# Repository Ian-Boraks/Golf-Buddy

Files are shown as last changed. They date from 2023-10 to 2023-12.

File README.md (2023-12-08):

- [Overview](#overview)
  - [Project Photos](#project-photos)
    - [Launcher](#launcher)
    - [Hole](#hole)
- [Hardware](#hardware)
  - [BOM](#bom)
  - [CAD](#cad)
    - [Laser Cut Parts](#laser-cut-parts)
  - [Electronics](#electronics)
    - [Wiring Diagram Launcher](#wiring-diagram-launcher)
    - [Wiring Diagram Hole](#wiring-diagram-hole)
- [Development](#development)
  - [RFID](#rfid)
    - [Code Snippets](#code-snippets)
  - [Launcher](#launcher-1)
    - [Code Snippets](#code-snippets-1)
  - [Hole](#hole-1)
    - [Code Snippets](#code-snippets-2)
- [Skills Beyond](#skills-beyond)
  - [Fernando](#fernando)
  - [Ian](#ian)

---

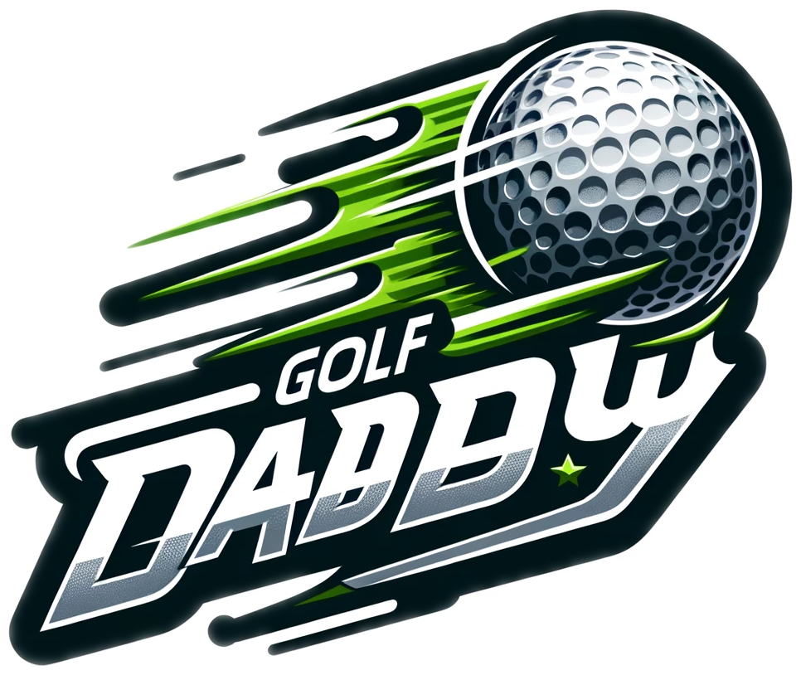
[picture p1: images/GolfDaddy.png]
Golf Buddy


[Demo Video (https://youtu.be/wagic4B7uYY)](https://youtu.be/wagic4B7uYY)
[RFID Video (https://youtu.be/jHi_h-PA1bc)](https://youtu.be/jHi_h-PA1bc)

# Overview

Welcome to the project documentation for an innovative addition to the world of mini golf: a High-Speed Golf Ball Shooter. This project began with a simple yet ambitious goal: to enhance the traditional golfing experience, particularly in the realm of putting. Our initial vision was to develop a tool that would assist golfers in refining their putting skills in a competitive and engaging manner. However, as we delved deeper into the project, our focus shifted, leading us to a more dynamic and playful interpretation of golfing aids.

**Main Reasons for Project Shift:**

1. Our motor was too powerful for the golf ball. We were unable to tune the motor speed too produce reasonable ball speeds.
2. Our RFID reader was unable to read the RFID tags on the golf balls. We were unable to find a solution to this problem that would be cost feasible with our limited budget.
3. The ball return mechanism was too complex for our limited time frame.

## Project Photos

### Launcher

\
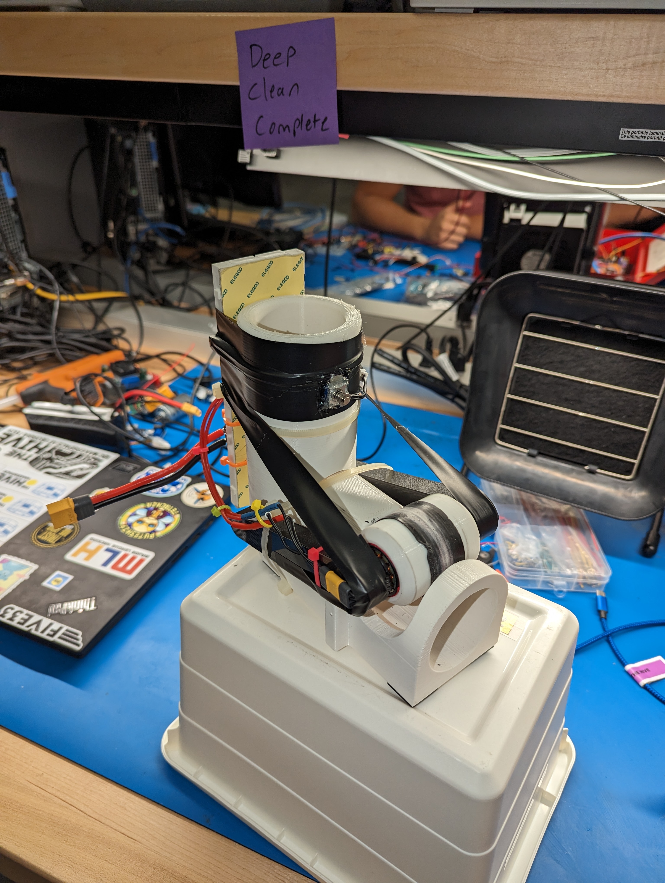
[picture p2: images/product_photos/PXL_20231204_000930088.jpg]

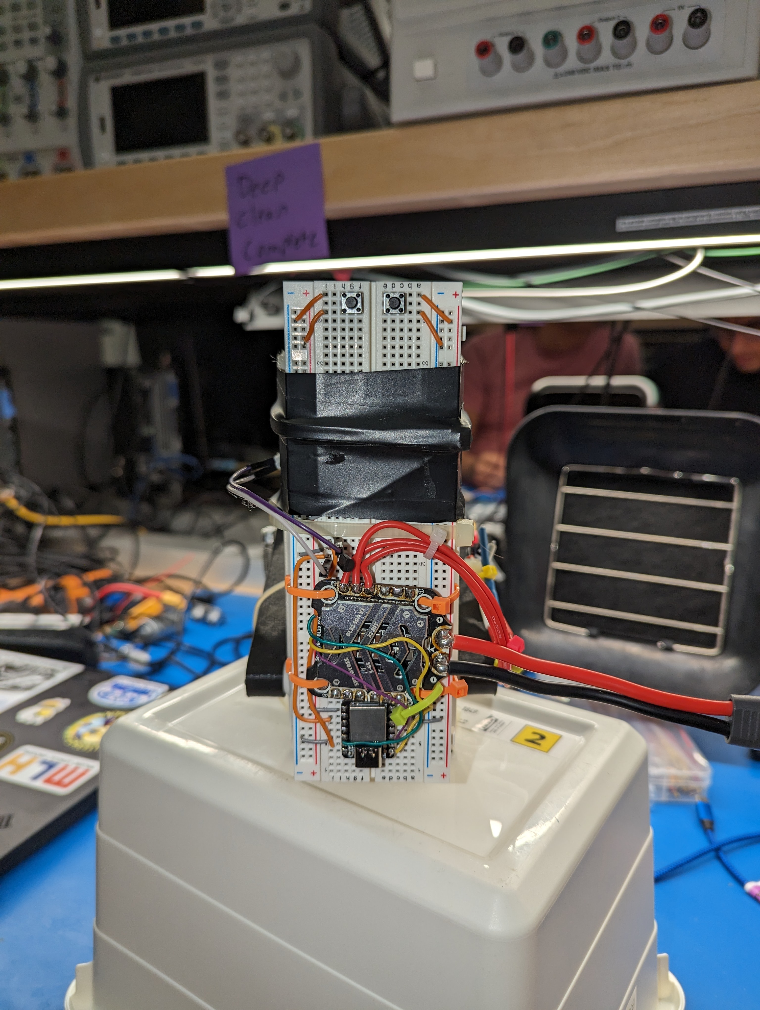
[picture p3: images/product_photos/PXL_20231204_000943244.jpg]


### Hole

\
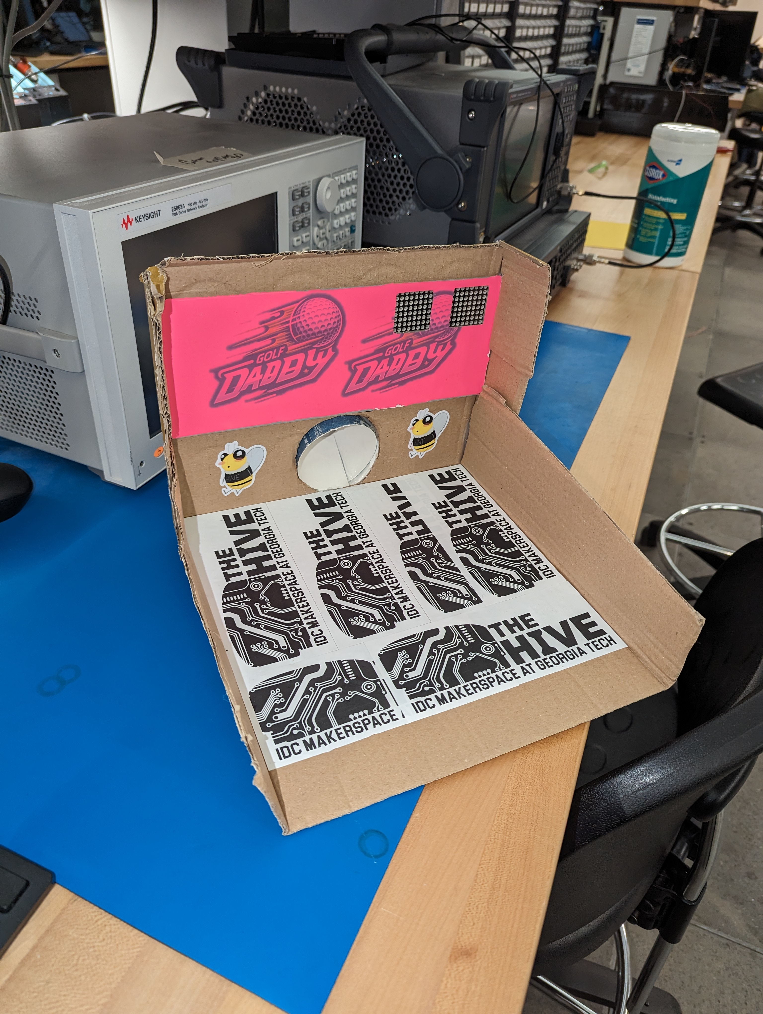
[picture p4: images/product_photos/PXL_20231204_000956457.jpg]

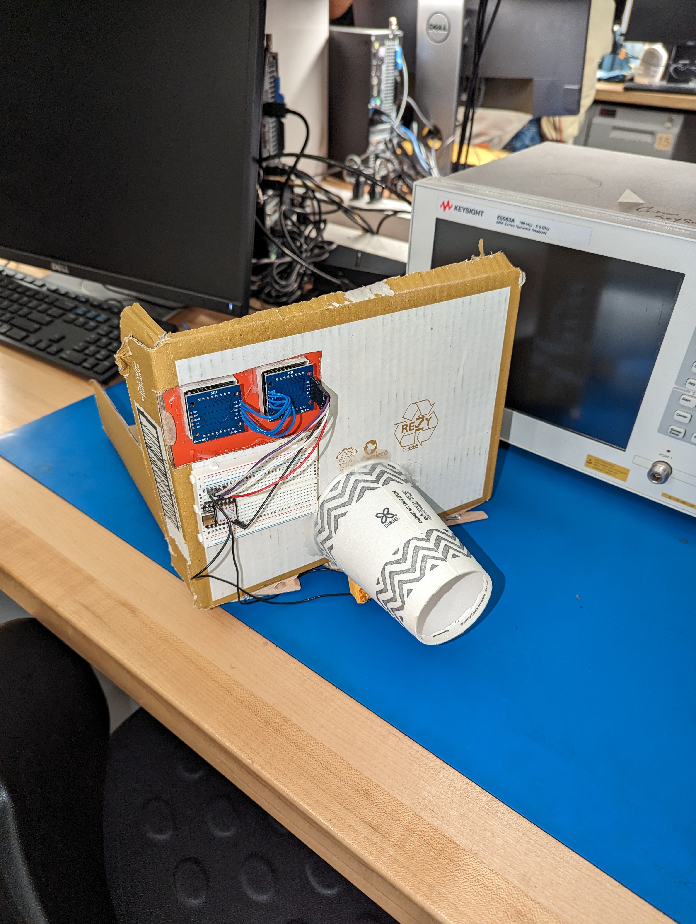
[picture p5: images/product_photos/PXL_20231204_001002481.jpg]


# Hardware

## BOM

| Part | Quantity | Price  |
| --- | --- | --- |
| Seeduino Xiao | 2 | $5.90  |
| NeoPixel Matrix  | 2 | $9.95  |
| 6s LiPo Battery  | 1 | $30.00 |
| ESC SpeedyBee | 1 | $60.00 |
| Bearings | 4 | $10.00 |
| 3D Printed Parts | 1 | ~~~ |
| Limit Switch | 2 | $5.00  |
| Switches | 2 | $5.00  |
| Microphone | 1 | $5.00  |

## CAD

**Launcher**: \
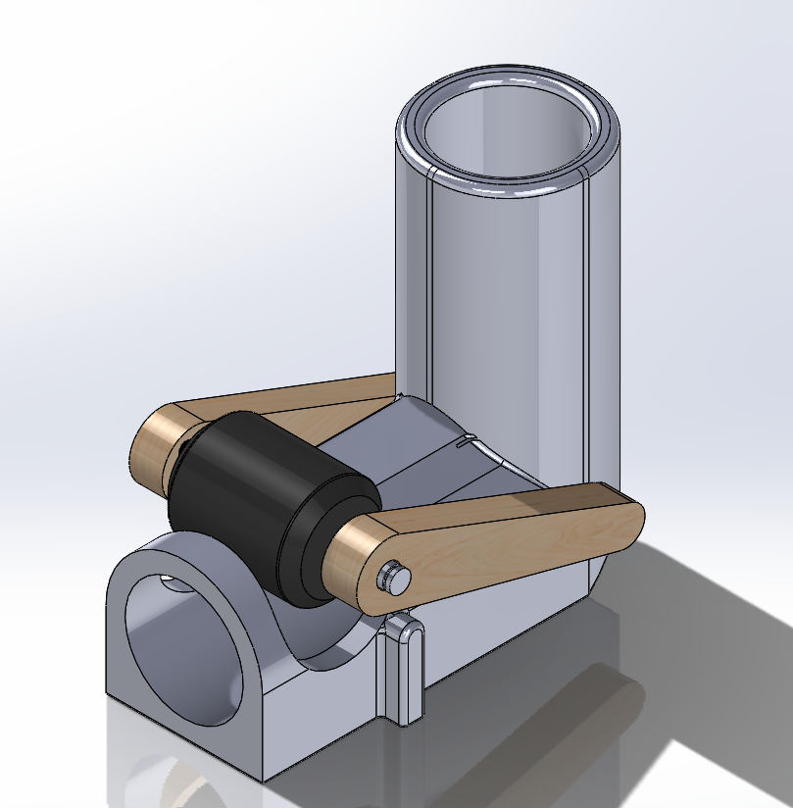
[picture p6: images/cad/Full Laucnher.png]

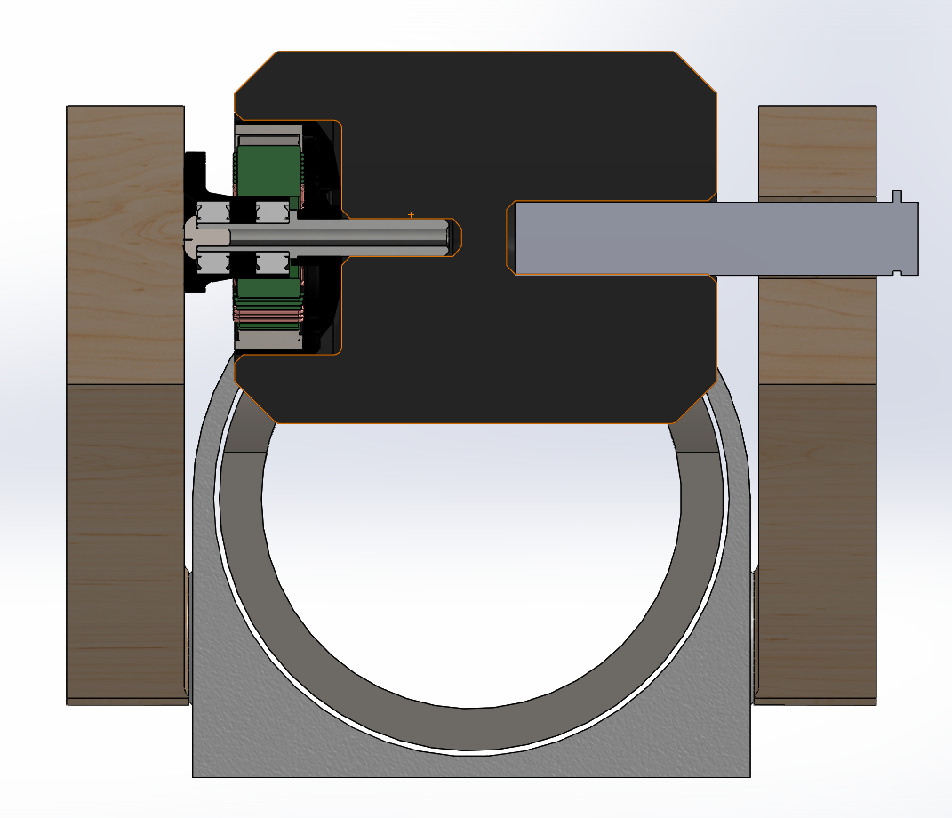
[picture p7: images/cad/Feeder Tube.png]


### Laser Cut Parts

**Hole Plate**: \
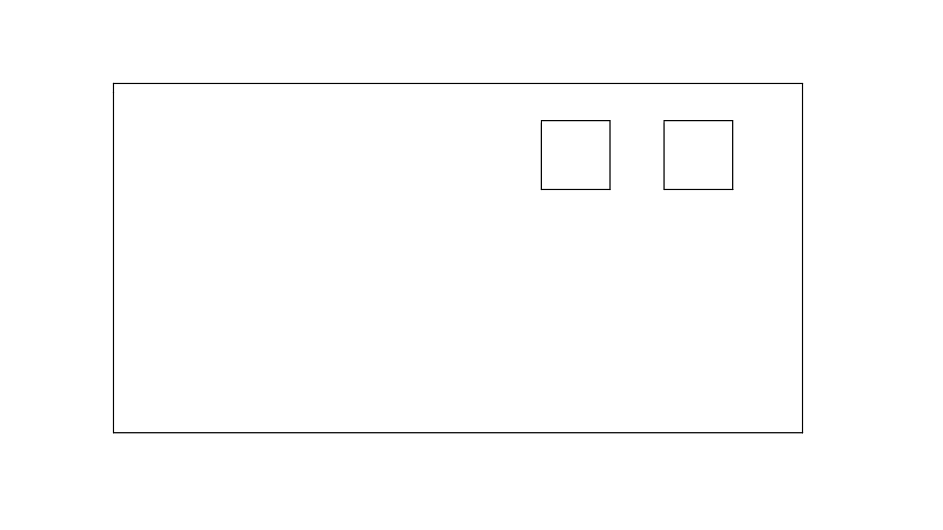
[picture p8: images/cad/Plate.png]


## Electronics

### Wiring Diagram Launcher

Wiring Diagram

### Wiring Diagram Hole

Wiring Diagram

# Development

## RFID

[RFID Video (https://youtu.be/jHi_h-PA1bc)](https://youtu.be/jHi_h-PA1bc)

The original idea was to use the RFID tags embedded into the balls to read the player's score. Initial testing with the RFID was positive, as it could read different tags with different point values and add them. \
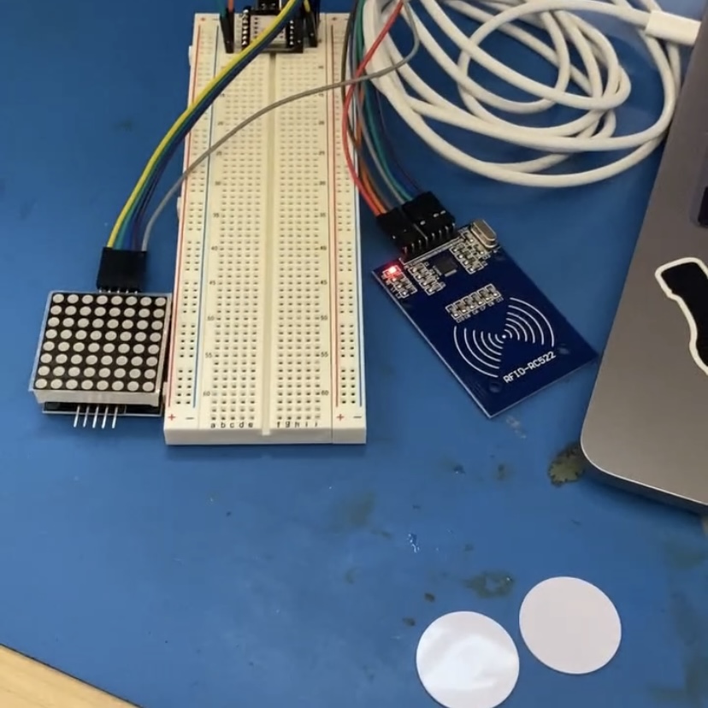
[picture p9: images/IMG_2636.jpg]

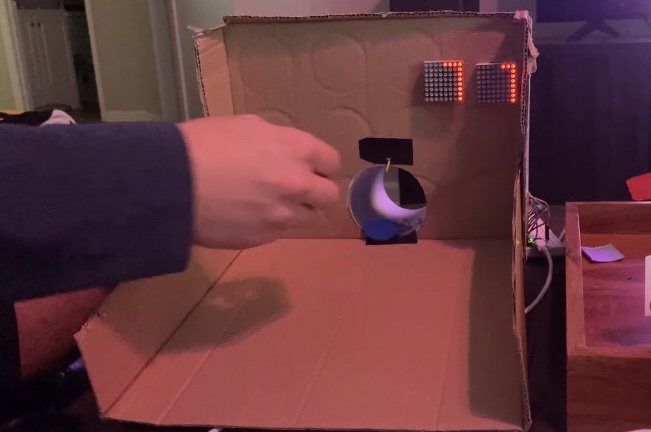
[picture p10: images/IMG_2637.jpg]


However, the issue arose during integration with the golf balls. The RFID was not strong enough to travel through the golf ball to get consistent readings. The issue only worsened with the launcher integration because the ball traveled too fast to be read. The RFID hardware needed to be changed with something that could be more reliable and work at faster speeds. The change to limit swithces proved to be very reliable and work on any speed we tested because of the simplicity of the tech. The lessoned learned was to not overcomplicate things sometimes instead of trying to make a golf ball smart just add a simple button. \
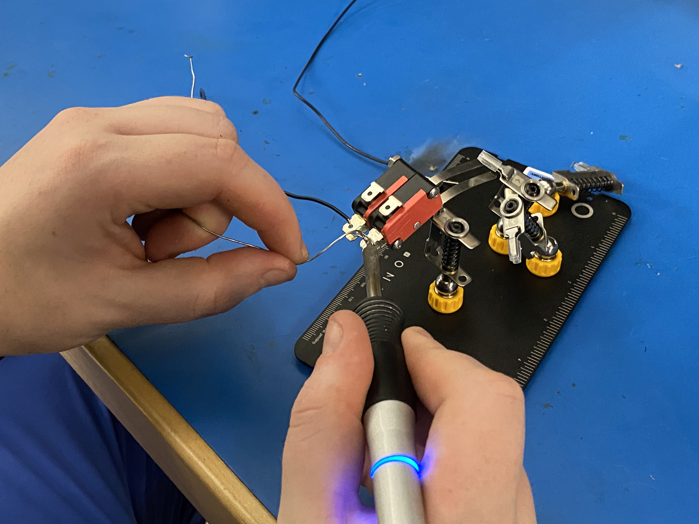
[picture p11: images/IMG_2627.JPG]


### Code Snippets

Even though RFID didn't get implemented into the final design. A lot of effort went into the development of the RFID tracking system.

```cpp
#include <SPI.h>
#include <MFRC522.h>
#include <MD_MAX72xx.h>

//DOT Matrix Setup
#define HARDWARE_TYPE MD_MAX72XX::GENERIC_HW

#define MAX_DEVICES 1
#define CS_PIN 6
#define  DELAYTIME  50
MD_MAX72XX mx = MD_MAX72XX(HARDWARE_TYPE, CS_PIN, MAX_DEVICES);

//RFID Scanner Setup
#define RST_PIN         5          // Configurable, see typical pin layout above
#define SS_PIN          7         // Configurable, see typical pin layout above
MFRC522 mfrc522(SS_PIN, RST_PIN);  // Create MFRC522 instance

byte readCard[4];
const char* rfidTags[] = {"931D7CD", "492561", "4A23E1","451421"};
int tagPoints[] = {1,2,3,4};
String tagID = "";
int points = 0;

void setup() {
  // put your setup code here, to run once:

  Serial.begin(9600);		// Initialize serial communications with the PC
	while (!Serial);		// Do nothing if no serial port is opened (added for Arduinos based on ATMEGA32U4)
	SPI.begin();			// Init SPI bus
	mfrc522.PCD_Init();		// Init MFRC522
	delay(4);	
	mfrc522.PCD_DumpVersionToSerial();	// Show details of PCD - MFRC522 Card Reader details
  mx.begin();
  mx.control(MD_MAX72XX::INTENSITY, 0);
  mx.clear();
  Serial.println("Scan Card");

}

void loop() {

  //Wait until new tag is available
  while (getID()) {    

    //Search for Tag in dictonary 
    for(int i = 0; i < sizeof(rfidTags); i++) {
      if (tagID == rfidTags[i]) {
        points = points + tagPoints[i];
        Serial.print("TAG: ");
        Serial.println(tagID);

        Serial.print("Points: ");
        Serial.println(points);
        break;
      }
    }

    if (points >= 8) {
      Serial.println("WINNNER");
      win();
    
    } else {
      for(int i = 0; i < (points); i++) {
    
        //mx.setRow(i,0xff);
        mx.setColumn(i,0xff);
        delay(DELAYTIME);

      }

    }

    Serial.print("Total POINTS: ");
    Serial.println(points);
    delay(200);
  }

}

//Read new tag if available
boolean getID() {
  // Getting ready for Reading PICCs
  if ( ! mfrc522.PICC_IsNewCardPresent()) { //If a new PICC placed to RFID reader continue
  //Serial.println("NEWCARD");
  return false;
  }
  if ( ! mfrc522.PICC_ReadCardSerial()) { //Since a PICC placed get Serial and continue
  //Serial.println("READCARD");
  return false;
  }
  tagID = "";
  for ( uint8_t i = 0; i < 4; i++) { // The MIFARE PICCs that we use have 4 byte UID
  //readCard[i] = mfrc522.uid.uidByte[i];
  tagID.concat(String(mfrc522.uid.uidByte[i], HEX)); // Adds the 4 bytes in a single String variable
  }
  tagID.toUpperCase();
  mfrc522.PICC_HaltA(); // Stop reading
  return true;
}

void win() {
  points = 0;

  for (int i = 0; i < 3; i++) {
    int  rmin = 0, rmax = ROW_SIZE-1;
    int  cmin = 0, cmax = (COL_SIZE*MAX_DEVICES)-1;

    mx.clear();
    while ((rmax > rmin) && (cmax > cmin))
    {
      // do row
      for (int i=cmin; i<=cmax; i++)
      {
        mx.setPoint(rmin, i, true);
        delay(DELAYTIME/MAX_DEVICES);
      }
      rmin++;

      // do column
      for (uint8_t i=rmin; i<=rmax; i++)
      {
        mx.setPoint(i, cmax, true);
        delay(DELAYTIME/MAX_DEVICES);
      }
      cmax--;

      // do row
      for (int i=cmax; i>=cmin; i--)
      {
        mx.setPoint(rmax, i, true);
        delay(DELAYTIME/MAX_DEVICES);
      }
      rmax--;

      // do column
      for (uint8_t i=rmax; i>=rmin; i--)
      {
        mx.setPoint(i, cmin, true);
        delay(DELAYTIME/MAX_DEVICES);
      }
      cmin++;
    }
  }
  
  mx.clear();
}

```

---

## Launcher

The original design of the launcher was a tube that would need an additional feeder tube to function. The issue with this design was that the ball would get stuck in the feeder tube and not be able to be launched. The solution was to change the design to a single tube that would be able to launch the ball without the need of a feeder tube.

**Launcher Initial Design**: \
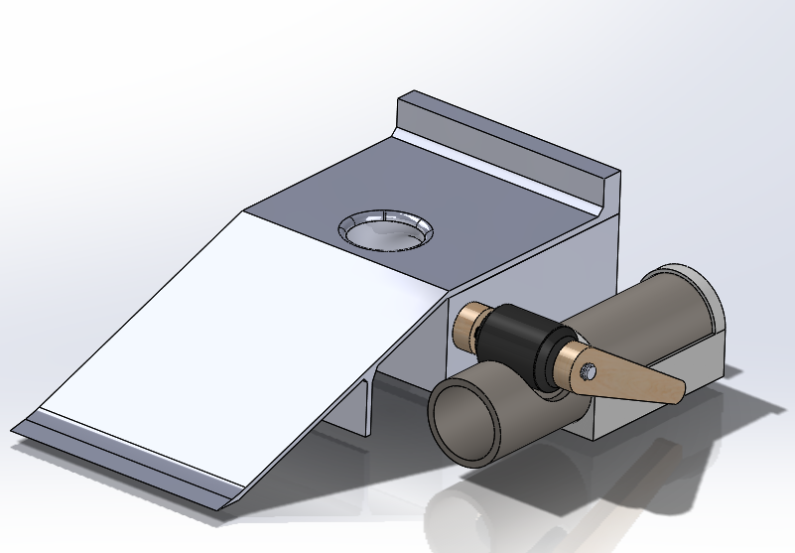
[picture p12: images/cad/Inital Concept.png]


**Launcher Final Design**: \


However, this design didn't allow enough balls to be loaded in and our project changed to a single ball launcher. At this point, we decided to completely pivot from a putting assistant to a fun golf ball launcher. The lesson learned was to not be afraid to change the design if it doesn't work.

The final pivot point was the addition of a miss counter. This is done via a mic on the back of the device that can track if the user misses. This allows us to re-gamify the system and add a competitive aspect to the game.

### Code Snippets

**ESC Arming**:

The most difficult part of the launcher code was the arming of the ESC. This required us to go through the BLHELI_32 documentation and codebase to figure out the specific commands to send to the ESC. The code below is the final code that we used to arm the ESC.\
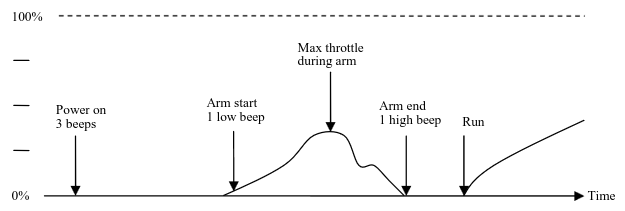
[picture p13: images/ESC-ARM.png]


```c++
Motor.attach(0);

delay(100);

Motor.writeMicroseconds(0);
delayMicroseconds(400);
Motor.writeMicroseconds(1800);
delayMicroseconds(500);
Motor.writeMicroseconds(1000);
```

---

## Hole



### Code Snippets

**Pixel Matrix**: \
The pixel matrix output is done via two ways.

1. Manually setting each row / col.
   1. The `win()` and `updatePoints()` functions use this method.
2. Using a custom `updateDisplay()` function.
   1. Other functions like `dissolve()`, `displayNumberOne()`, and `displayNumberTwo()` all use this update function.

The `updateDisplay()` function is as follows:

```cpp
void updateDisplay(bool matrix[][COL_SIZE])
{
  for (int r = 0; r < ROW_SIZE; r++)
  {
    for (int c = 0; c < COL_SIZE; c++)
    {
      mx.setPoint(r, c, matrix[r][c]);
    }
  }
}
```

**Score Tracking (Microphone)**: \
Below is the code used to detect if the player missed their shot. It is a simple system that pulls the microphone to see if it drop below its volume threshold.

```c++
#define VOLUME_THRESHOLD 20
while (digitalRead(button))
  {
    int sound = analogRead(mic);
    if (sound < VOLUME_THRESHOLD)
    {
        hits++;
        delay(500);
        Serial.print("HIT: ");
        Serial.println(sound);

        points++;

        updatePoints();
    }

    if (hits >= 16)
    {
        break;
    }
  }
```

# Skills Beyond

## Fernando

- Laser cutting metal using the fablight in The Hive
- Programming on a Seeed Studio XIAO SAMD21 mircocontroller
- Using multiple SPI devices

## Ian

- Laser cutting metal using the fablight in The Hive
- Doing manual brushless motor control
- Sublimation printing

<!--
# Special Thanks

We would like to thank the following people for their contributions to this project:

Our ambassador and visionary, Golf Daddy:

<img src="/images/ambassador.jpg" width=300 height=300>

Golf Daddy helped us and supported us through the initial stages of this project. He provided us with the inspiration and motivation to pursue this project, and we are forever grateful for his guidance. But in all seriousness, he did help bring our spirits up by playing guitar during our long nights at the HIVE.
-->

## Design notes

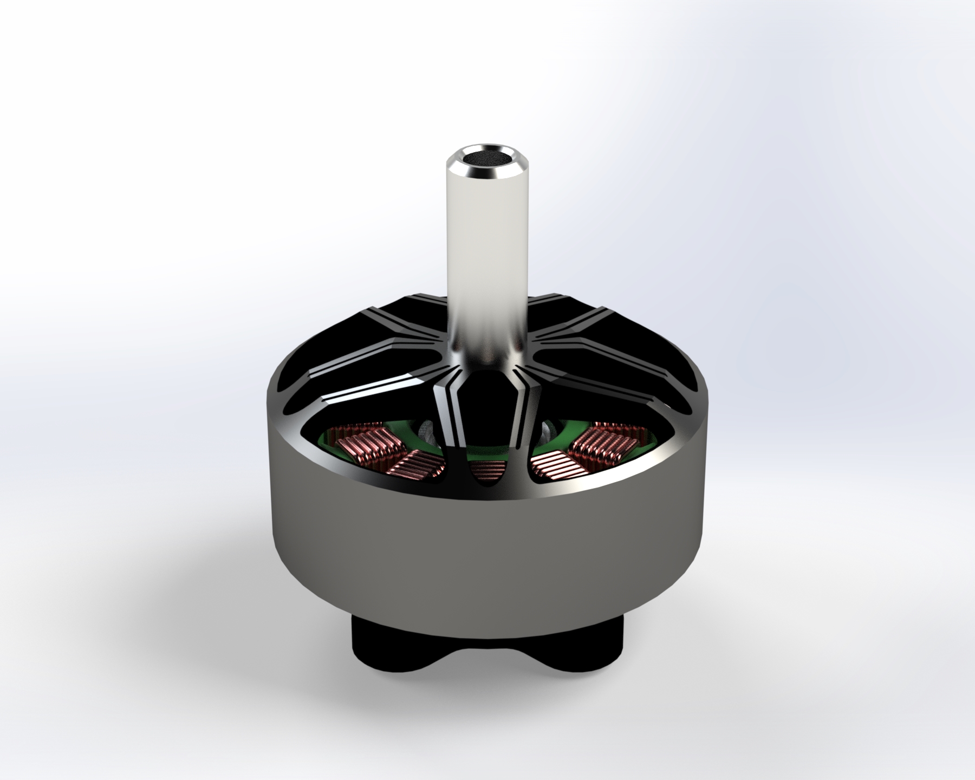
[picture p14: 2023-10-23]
CAD/RCinPOWER GTS-V2 2207Plus (Grey-Black)/Renders/GTS-V2 (Black-Grey).jpg

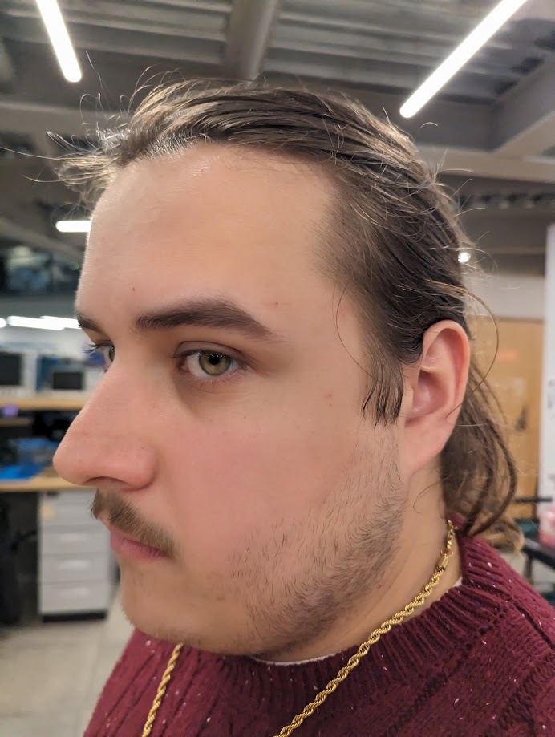
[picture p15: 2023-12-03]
images/ambassador.jpg

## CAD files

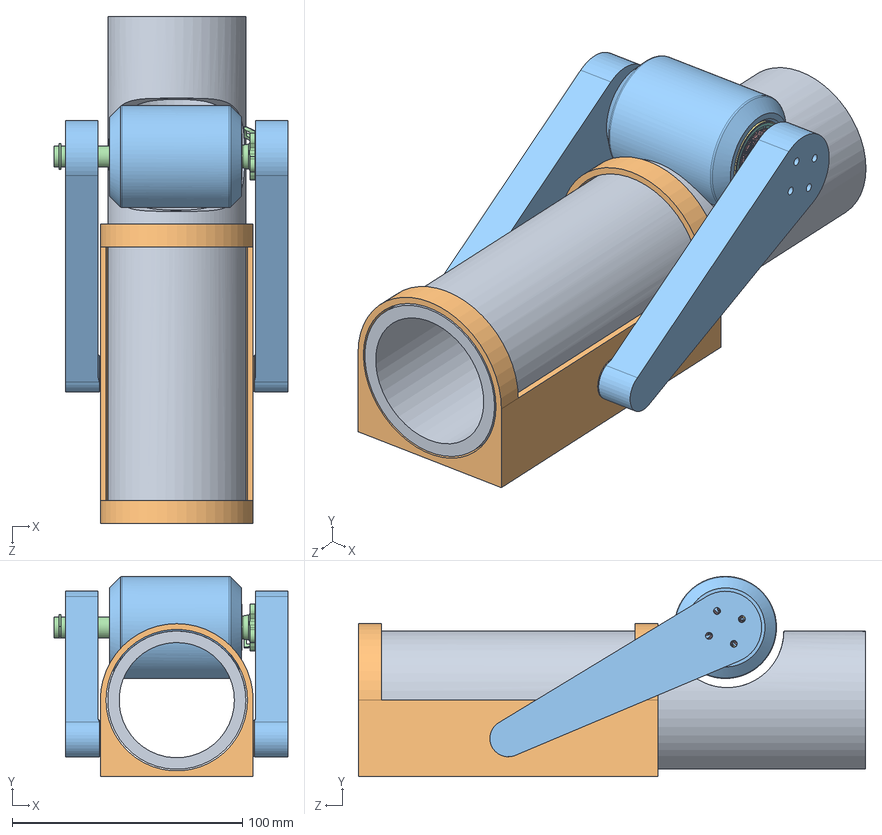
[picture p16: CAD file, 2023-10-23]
CAD/GolfDaddy.SLDASM
101.4 x 86.9 x 220.0 mm
Part1^GolfDaddy
Part2^GolfDaddy
Part3^GolfDaddy
Base
Stator
Shaft
Bell
Magnet Assembly
Bearing x 2
M3x4
Part4^GolfDaddy
Part5^GolfDaddy

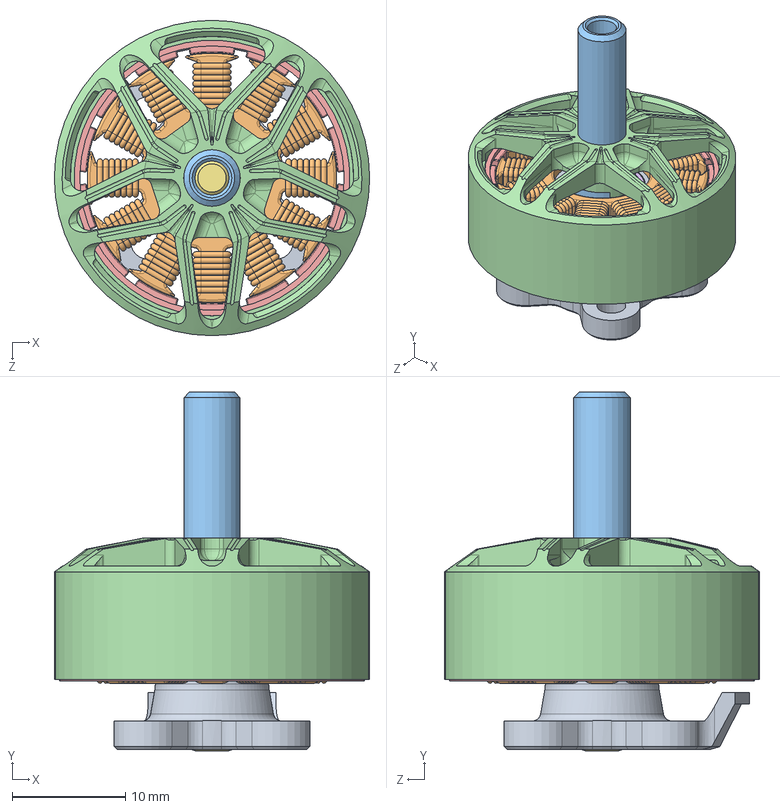
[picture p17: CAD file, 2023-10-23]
CAD/RCinPOWER GTS-V2 2207Plus (Grey-Black)/GTS-V2 2207Plus.SLDASM
27.8 x 31.6 x 27.8 mm
Base
Stator
Shaft
Bell
Magnet Assembly
Bearing x 2
M3x4

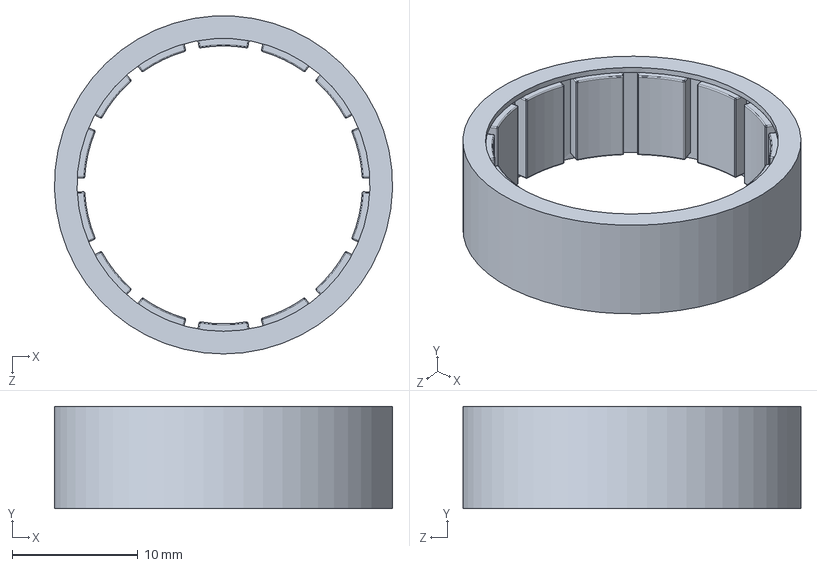
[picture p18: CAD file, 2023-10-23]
CAD/RCinPOWER GTS-V2 2207Plus (Grey-Black)/Magnet Assembly.SLDPRT
26.9 x 8.14 x 26.9 mm

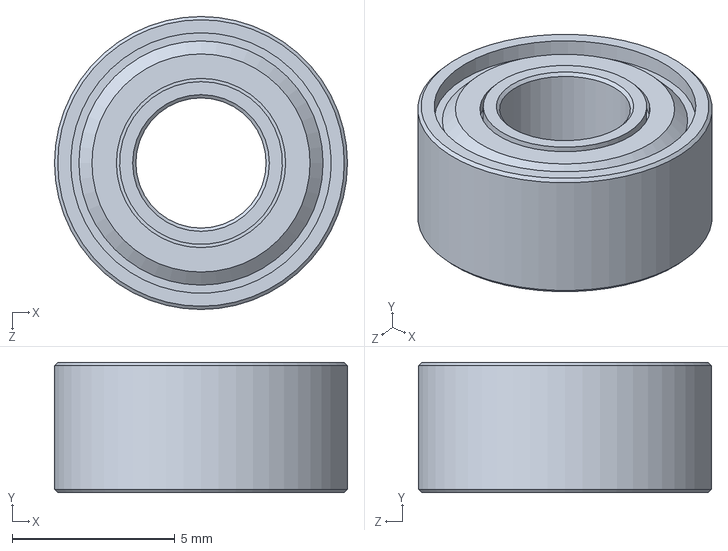
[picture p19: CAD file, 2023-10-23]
CAD/RCinPOWER GTS-V2 2207Plus (Grey-Black)/Bearing.SLDPRT
9.00 x 4.00 x 9.00 mm

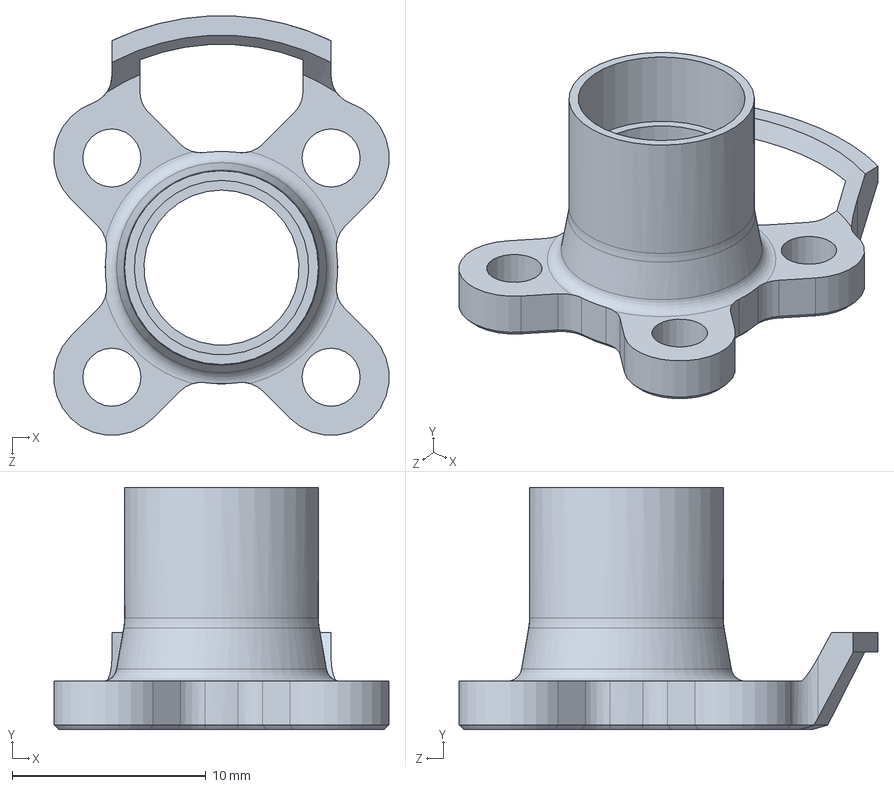
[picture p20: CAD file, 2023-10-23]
CAD/RCinPOWER GTS-V2 2207Plus (Grey-Black)/Base.SLDPRT
17.3 x 12.5 x 21.6 mm

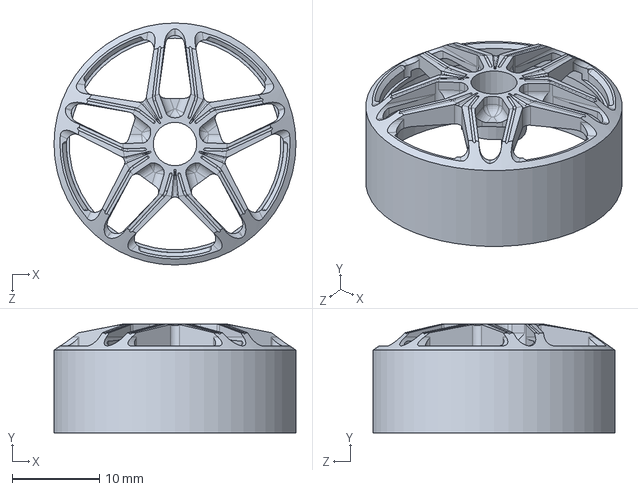
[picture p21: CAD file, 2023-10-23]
CAD/RCinPOWER GTS-V2 2207Plus (Grey-Black)/Bell.SLDPRT
27.8 x 12.5 x 27.8 mm

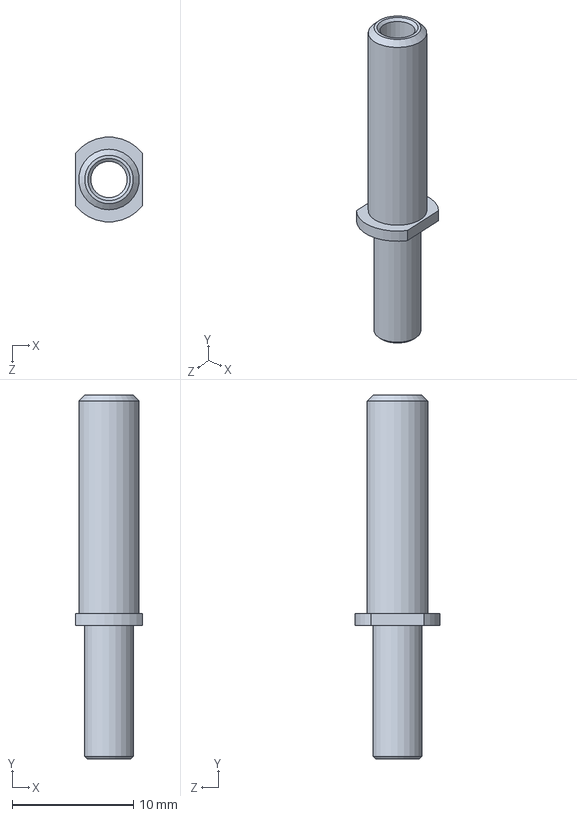
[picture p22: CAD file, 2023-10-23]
CAD/RCinPOWER GTS-V2 2207Plus (Grey-Black)/Shaft.SLDPRT
5.50 x 30.0 x 6.96 mm

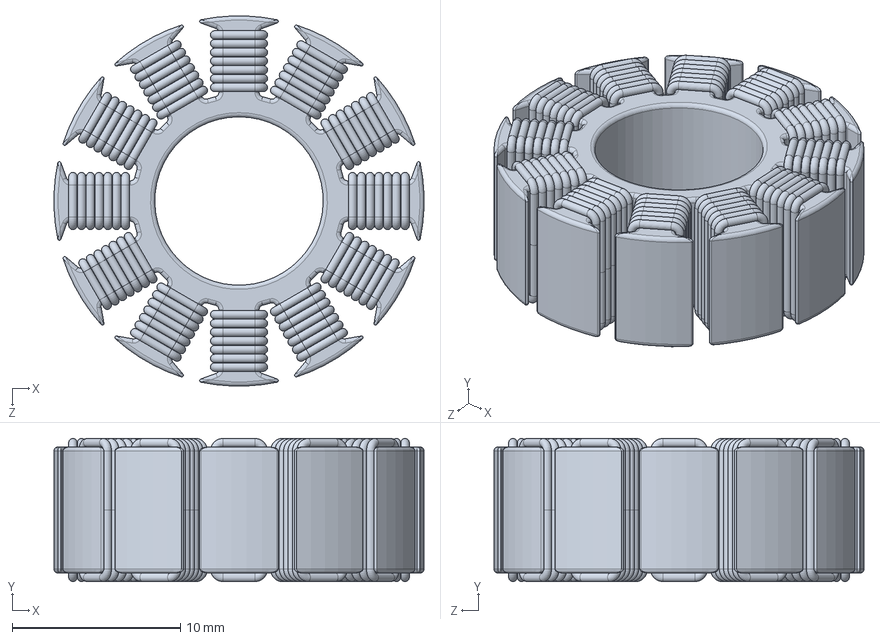
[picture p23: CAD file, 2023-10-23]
CAD/RCinPOWER GTS-V2 2207Plus (Grey-Black)/Stator.SLDPRT
22.0 x 8.50 x 22.0 mm

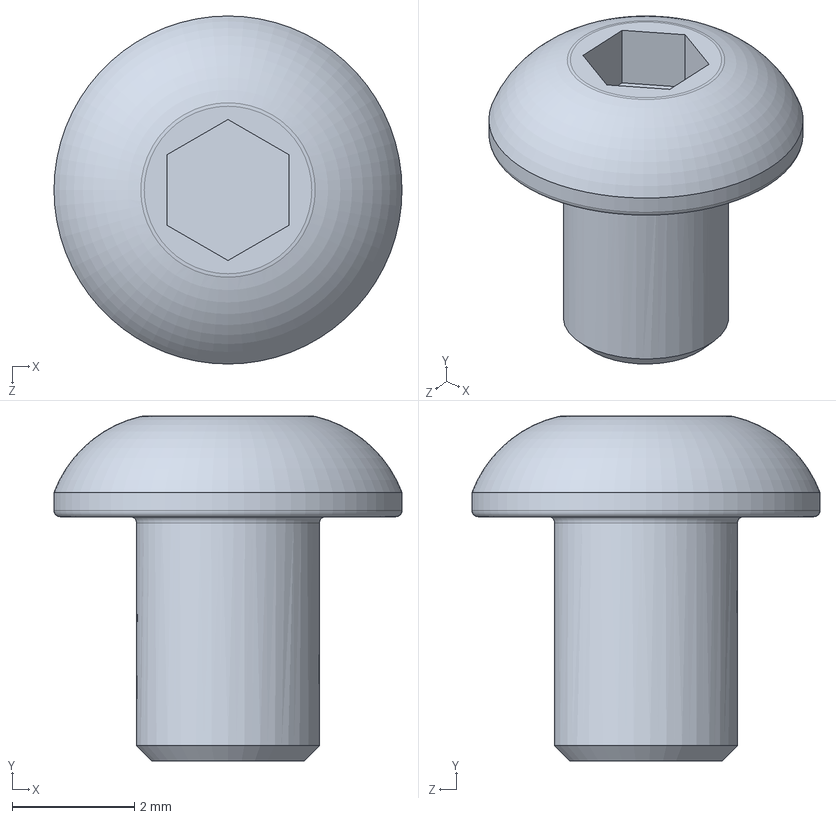
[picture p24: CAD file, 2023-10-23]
CAD/RCinPOWER GTS-V2 2207Plus (Grey-Black)/M3x4.SLDPRT
5.70 x 5.65 x 5.70 mm

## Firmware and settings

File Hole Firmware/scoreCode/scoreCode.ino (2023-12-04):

#include <SPI.h>
#include <MFRC522.h>
#include <MD_MAX72xx.h>
#include <cstdlib> // For rand() and srand()
#include <ctime>   // For time()

// DOT Matrix Setup
#define HARDWARE_TYPE MD_MAX72XX::GENERIC_HW

#define MAX_DEVICES 1
#define CS_PIN 6
#define DELAYTIME 50
MD_MAX72XX mx = MD_MAX72XX(HARDWARE_TYPE, CS_PIN, MAX_DEVICES);

// //RFID Scanner Setup
// #define RST_PIN         5          // Configurable, see typical pin layout above
// #define SS_PIN          7         // Configurable, see typical pin layout above
// MFRC522 mfrc522(SS_PIN, RST_PIN);  // Create MFRC522 instance

// Limit swith
#define button 5
int buttonState = 1;

#define mic 7
int hits = 0;

bool gameOver = false;
bool player = true;

int playerOnePoints = 0;
int playerTwoPoints = 0;

byte readCard[4];
const char *rfidTags[] = {"931D7CD", "492561", "4A23E1", "451421"};
int tagPoints[] = {1, 2, 3, 4};
String tagID = "";
int points = 0;

void setup()
{
  // put your setup code here, to run once:

  // Serial.begin(9600); // Initialize serial communications with the PC
  // while (!Serial)
  // ;          // Do nothing if no serial port is opened (added for Arduinos based on ATMEGA32U4)
  SPI.begin(); // Init SPI bus

  pinMode(button, INPUT_PULLUP);
  pinMode(mic, INPUT);

  // mfrc522.PCD_Init();		// Init MFRC522
  // delay(4);
  // mfrc522.PCD_DumpVersionToSerial();	// Show details of PCD - MFRC522 Card Reader details
  mx.begin();
  mx.control(MD_MAX72XX::INTENSITY, 0);
  mx.clear();
  Serial.println("Scan Card");
}

void updatePoints()
{
  for (int i = 0; i < min(points, 8); i++)
  {
    mx.setColumn(i, 0xf0);
    delay(DELAYTIME);
  }

  for (int i = points - 8; i < min(points, 16); i++)
  {
    mx.setColumn(i - 8, 0xff);
    delay(DELAYTIME);
  }
}

void loop()
{
  gameOver = false;
  hits = 0;
  points = 0;

  if (player)
  {
    displayNumberOne();
  }
  else
  {
    displayNumberTwo();
  }

  delay(5000);
  dissolve();

  while (digitalRead(button))
  {
    int sound = analogRead(mic);
    if (sound < 20)
    {
      hits++;
      delay(500);
      Serial.print("HIT: ");
      Serial.println(sound);

      points++;

      updatePoints();
    }

    if (hits >= 16)
    {
      break;
    }
  }

  Serial.println(hits);
  delay(500);

  Serial.print("Total POINTS: ");
  Serial.println(points);

  if (player)
  {
    playerOnePoints += points;
  }
  else
  {
    playerTwoPoints += points;
  }

  if (points < 16)
  {
    win();
  }
  else
  {
    dissolve();
  }

  if (!player)
  {
    Serial.print("Player 1: ");
    Serial.println(playerOnePoints);
    Serial.print("Player 2: ");
    Serial.println(playerTwoPoints);

    if (playerOnePoints < playerTwoPoints)
    {
      // Blink player 1
      for (int i = 0; i < 3; i++)
      {
        displayNumberOne();
        delay(500);
        mx.clear();
        delay(500);
      }
    }
    else if (playerOnePoints > playerTwoPoints)
    {
      // Blink player 2
      for (int i = 0; i < 3; i++)
      {
        displayNumberTwo();
        delay(500);
        mx.clear();
        delay(500);
      }
    }
    else
    {
      // Blink both
      for (int i = 0; i < 3; i++)
      {
        displayNumberOne();
        delay(500);
        mx.clear();
        delay(500);

        displayNumberTwo();
        delay(500);
        mx.clear();
        delay(500);
      }
    }

    playerOnePoints = 0;
    playerTwoPoints = 0;
  }

  player = !player;
}

void win()
{
  points = 0;

  int rmin = 0, rmax = ROW_SIZE - 1;
  int cmin = 0, cmax = (COL_SIZE * MAX_DEVICES) - 1;

  mx.clear();
  while ((rmax > rmin) && (cmax > cmin))
  {
    // do row
    for (int i = cmin; i <= cmax; i++)
    {
      mx.setPoint(rmin, i, true);
      delay(DELAYTIME / MAX_DEVICES);
    }
    rmin++;

    // do column
    for (uint8_t i = rmin; i <= rmax; i++)
    {
      mx.setPoint(i, cmax, true);
      delay(DELAYTIME / MAX_DEVICES);
    }
    cmax--;

    // do row
    for (int i = cmax; i >= cmin; i--)
    {
      mx.setPoint(rmax, i, true);
      delay(DELAYTIME / MAX_DEVICES);
    }
    rmax--;

    // do column
    for (uint8_t i = rmax; i >= rmin; i--)
    {
      mx.setPoint(i, cmin, true);
      delay(DELAYTIME / MAX_DEVICES);
    }
    cmin++;
  }

  mx.clear();
}

// Function to update the display based on the matrix state
void updateDisplay(bool matrix[][COL_SIZE])
{
  for (int r = 0; r < ROW_SIZE; r++)
  {
    for (int c = 0; c < COL_SIZE; c++)
    {
      mx.setPoint(r, c, matrix[r][c]);
    }
  }
}

void dissolve()
{
  // Assuming ROW_SIZE and COL_SIZE are defined elsewhere
  bool matrix[ROW_SIZE][COL_SIZE];

  // Initialize all points to true (on)
  for (int r = 0; r < ROW_SIZE; r++)
  {
    for (int c = 0; c < COL_SIZE; c++)
    {
      matrix[r][c] = true;
    }
  }

  // Update the display with the initial state
  updateDisplay(matrix);

  // Total number of points
  int totalPoints = ROW_SIZE * COL_SIZE;
  srand(time(NULL)); // Seed for random number generation

  while (totalPoints > 0)
  {
    // Generate a random row and column
    int r = rand() % ROW_SIZE;
    int c = rand() % COL_SIZE;

    // If the point is already off, continue
    if (!matrix[r][c])
      continue;

    // Turn off the point
    matrix[r][c] = false;
    totalPoints--;

    // Update the display
    updateDisplay(matrix);

    // Delay to visualize the effect
    delay(DELAYTIME);
  }
}

void displayNumberOne()
{
  bool numberOne[8][8] = {{0, 0, 0, 0, 0, 0, 0, 0},
                          {0, 0, 0, 0, 0, 0, 0, 0},
                          {1, 0, 0, 0, 0, 0, 0, 0},
                          {1, 0, 0, 0, 0, 0, 0, 0},
                          {1, 1, 1, 1, 1, 1, 1, 1},
                          {1, 0, 0, 0, 0, 0, 1, 0},
                          {0, 0, 0, 0, 0, 1, 0, 0},
                          {0, 0, 0, 0, 0, 0, 0, 0}};

  mx.clear(); // Clear the matrix
  updateDisplay(numberOne);
}

void displayNumberTwo()
{
  bool numberTwo[8][8] = {{0, 0, 0, 0, 0, 0, 0, 0},
                          {0, 1, 0, 0, 1, 1, 1, 1},
                          {0, 1, 0, 0, 1, 0, 0, 1},
                          {0, 1, 0, 0, 1, 0, 0, 1},
                          {0, 1, 0, 0, 1, 0, 0, 1},
                          {0, 1, 0, 0, 1, 0, 0, 1},
                          {0, 1, 1, 1, 1, 0, 0, 1},
                          {0, 0, 0, 0, 0, 0, 0, 0}};

  mx.clear(); // Clear the matrix
  updateDisplay(numberTwo);
}

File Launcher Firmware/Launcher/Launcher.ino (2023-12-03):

 #include <Servo.h>

Servo Motor;

#define motorButton 8
#define dropButton 4
#define dropBar 9


int motorSpeed = 1200;

volatile bool ballReady = false;

void setup() {
  Serial.begin(115200);

  pinMode(motorButton, INPUT_PULLUP);
  pinMode(dropButton, INPUT_PULLUP);
  pinMode(dropBar, OUTPUT);
  
  Motor.attach(0);

  delay(100);
  
  Motor.writeMicroseconds(0);
  delayMicroseconds(400);
  Motor.writeMicroseconds(1800);
  delayMicroseconds(500);
  Motor.writeMicroseconds(1000);
}

void updateMotor() {
  if (!digitalRead(motorButton)) {
    Motor.writeMicroseconds(motorSpeed);
  } else {
    Motor.writeMicroseconds(1040);
  }
}

void loop() {
  updateMotor();
  
  if (!digitalRead(dropButton)) {
    digitalWrite(13, HIGH);
    digitalWrite(dropBar, HIGH);
    Motor.writeMicroseconds(1040);

    int i = 0;
    for(;;) {
      digitalWrite(dropBar, HIGH);
      delay(1);
      
      updateMotor();

      if (i > 1000 && !digitalRead(dropButton)) break;
      if (++i > 10000) break;
    }

    digitalWrite(13, LOW);
    digitalWrite(dropBar, LOW);
    delay(500);
  }
}

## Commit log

2023-10-23 Add CAD
    [Base.SLDPRT, Bearing.SLDPRT, Bell.SLDPRT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]
2023-12-03 Base Code for the Score implimentation
    Uses the limit switches and dot display
2023-12-03 Added Electrical Work
    [Hole.kicad_pcb, Hole.kicad_sch, Launcher.kicad_pcb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]
2023-12-04 Photo Dump, Init
    [Hole.kicad_sch]
2023-12-04 Add PowerPoint
